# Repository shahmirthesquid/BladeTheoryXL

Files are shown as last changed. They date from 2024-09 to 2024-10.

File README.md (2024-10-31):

# BladeTheoryXL

Build log of my custom FPV drone built off an old Blade Theory XL
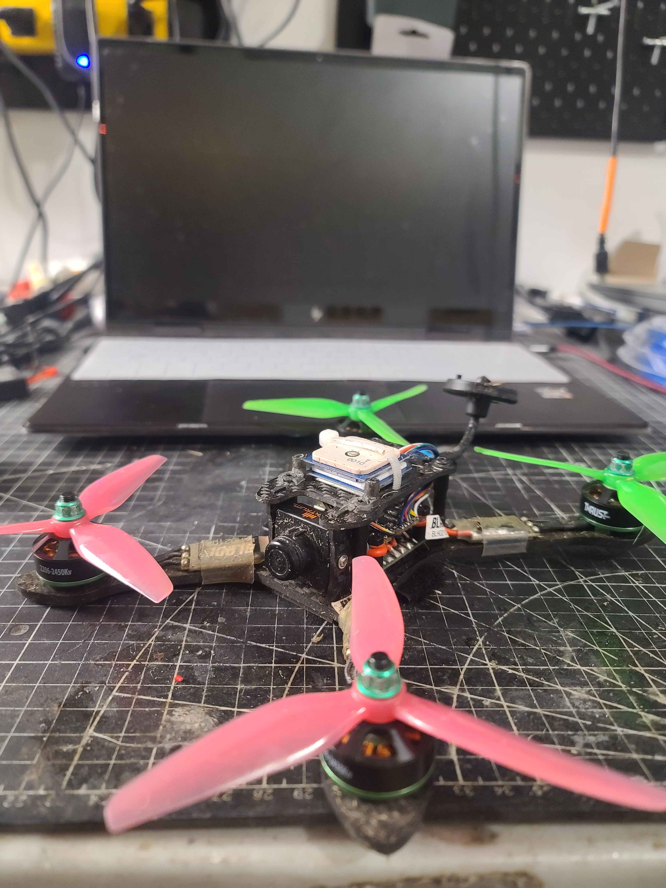
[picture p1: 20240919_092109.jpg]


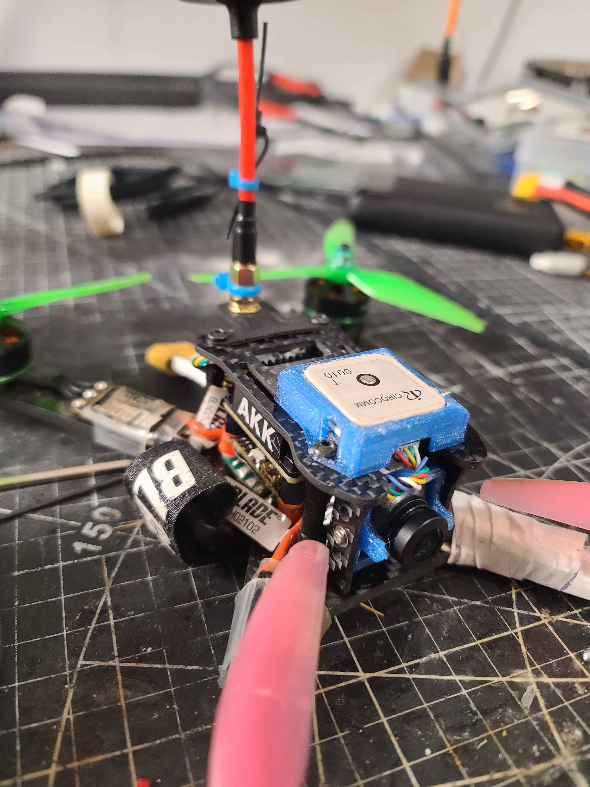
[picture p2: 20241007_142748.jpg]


https://www.bladehelis.com/product/theory-xl-5-fpv-bnf-basic/BLH02150.html

Archive of the above link can be found in this repo.

## Quick Overview

Frame: Blade Theory XL

Motors:Blade BLHA1023 Thrust Series 2206-2450Kv

ESC: 4 x Blade BLH02102 (FlyColor Fairy 30A)

Flight Controller: OMNIBUSF4SD w/ ICM42688P Gyro

VTX: AKK Ultra Long Range 3 Watt

Camera: Caddx Ratel 2

RX: SpeedyBee ELRS Nano

GPS: Beitan BN-880

Propellers: Ethix S3 Watermelon

Battery: 4S 1600mAh Lipo(10m Flight time) or 3S 4200mAh Molicel P42A pack (?m Flight time)

## Personal Tune and Config

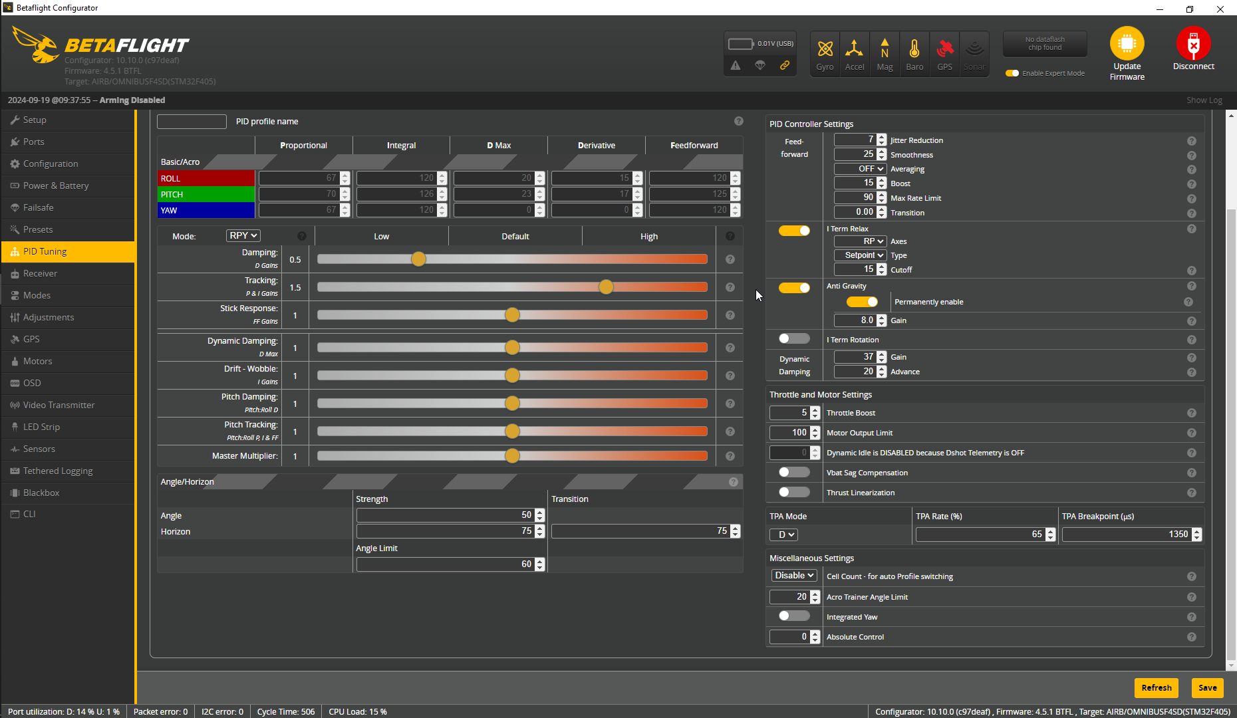
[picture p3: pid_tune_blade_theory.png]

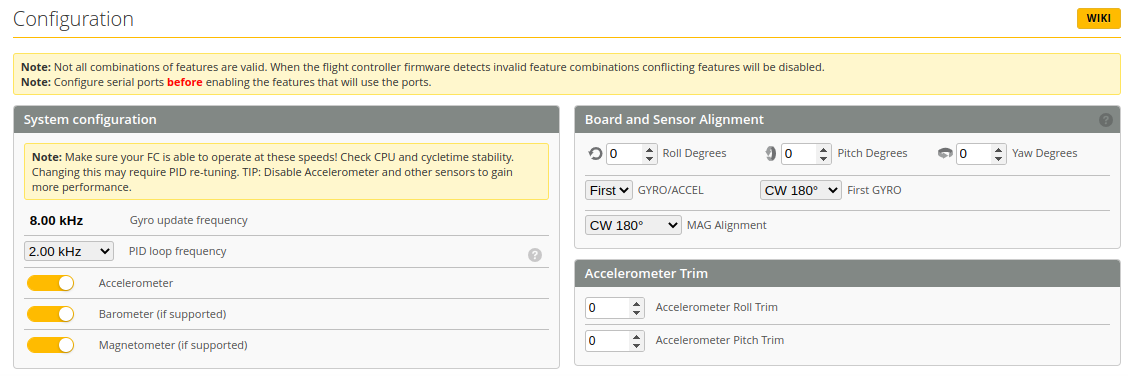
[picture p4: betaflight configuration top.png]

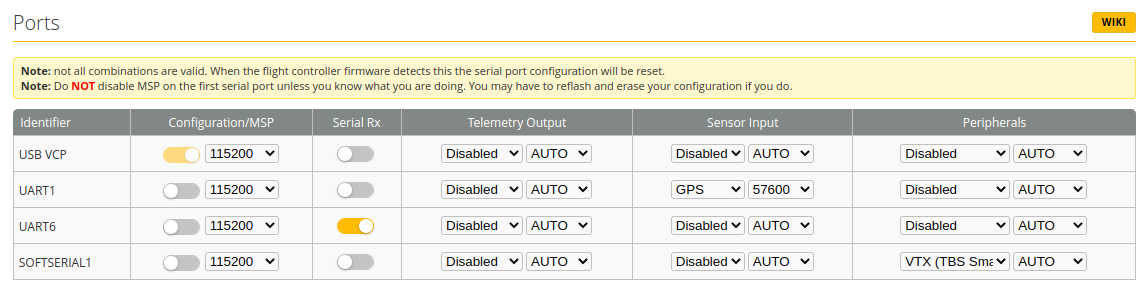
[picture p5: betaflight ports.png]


## Parts

### Frame
Stock 4mm carbon fiber Blade Theory XL frame.

### Flight Controller
Originally a Spektrum F3 controller but was replaced with F4V3S clone from aliexpress

https://www.aliexpress.com/item/1005005407722952.html



### Camera
Originally had a 700 TVL Spektrum camera. Wow this was such a bad camera. Terrible FOV and no OSD support.
Replacing with a CADDX Ratel 2. Currently waiting for it to arrive.

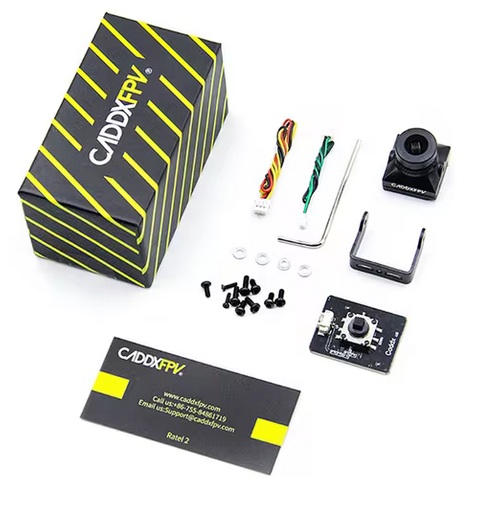
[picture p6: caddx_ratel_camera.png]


### Video Transmitter (VTX) 
Stock 200mw Spektrum VTX is actually quite nice. Range is very good for 200mw. Unfortunately you have to physically turn on the VTX button every flight. 

I am replacing this with AKK Long range 3W VTX. Currently waiting for it to arrive.

https://www.aliexpress.com/item/1005006955054449.html

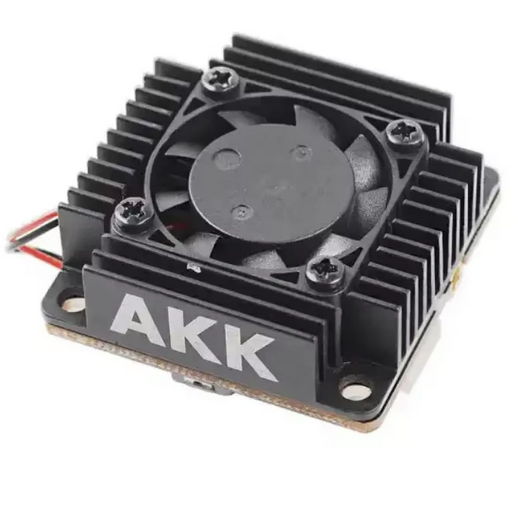
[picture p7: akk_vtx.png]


The AKK VTX seems really good. I put silicone conformal coating on it, and used SoftSerial to turn Motor5 pad into TX for the SmartAudio connection. I setup the VTX table, but had to manually set 5 bands in the table first. I then transferred the VTX switch settings from my Eachine Cvatar to be able to change VTX power using the 6 button switch at the top of my Jumper Tpro radio. 

Ultra Long Range VTX Table:
```
vtxtable channels 8
vtxtable band 1 BOSCAM_A A FACTORY 5865 5845 5825 5805 5785 5765 5745 5725
vtxtable band 2 BOSCAM_B B FACTORY 5733 5752 5771 5790 5809 5828 5847 5866
vtxtable band 3 BOSCAM_E E FACTORY 5705 5685 5665 0 5885 5905 0 0
vtxtable band 4 FATSHARK F FACTORY 5740 5760 5780 5800 5820 5840 5860 5880
vtxtable band 5 RACEBAND R FACTORY 5658 5695 5732 5769 5806 5843 5880 5917
vtxtable powerlevels 5
vtxtable powervalues 0 1 2 3 4
vtxtable powerlabels 250 500 1000 2000 3000
```

VTX Switch Based on Aux Channel 4:
```
vtx 0 3 0 0 1 1175 1375
vtx 1 3 0 0 2 1375 1525
vtx 2 3 0 0 3 1525 1650
vtx 3 3 0 0 5 1650 1850
```

This configuration changes VTX power based on the position of AUX channel 4. This skips the 2 watt setting on the VTX as I don't want to waste buttons to map out every power level. These buttons can then be reserved for future functionality.

### Reciever
Originally had a Spektrum SPM4649T / SH703X reciever that refused to go into bind mode.

Replaced with SpeedyBee ELRS Nano reciever from amazon

https://www.amazon.ca/dp/B0CTBWQ91P

### ESC
Stock power delivery board, and 30A BLHeli ESCS (BLH02102) running OneShot125 protocol.

ESCs are kinda bad, but after a custom tune they were alright. They didn't seem to have the precision of more modern ESCS using DSHOT protocol. 

I have the parts to replace these, but I'd like to ride these until they die so that I don't make ewaste.

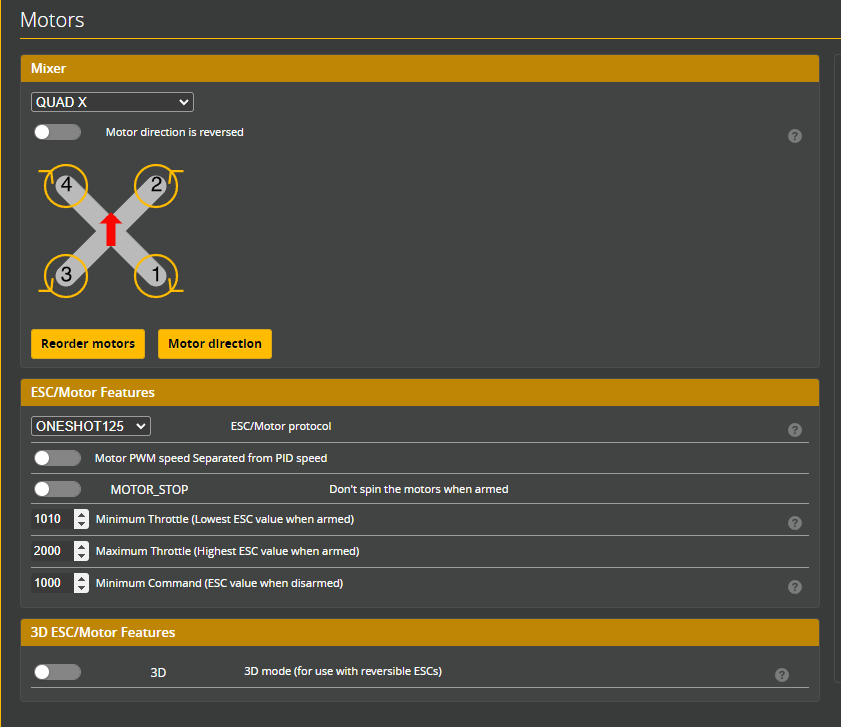
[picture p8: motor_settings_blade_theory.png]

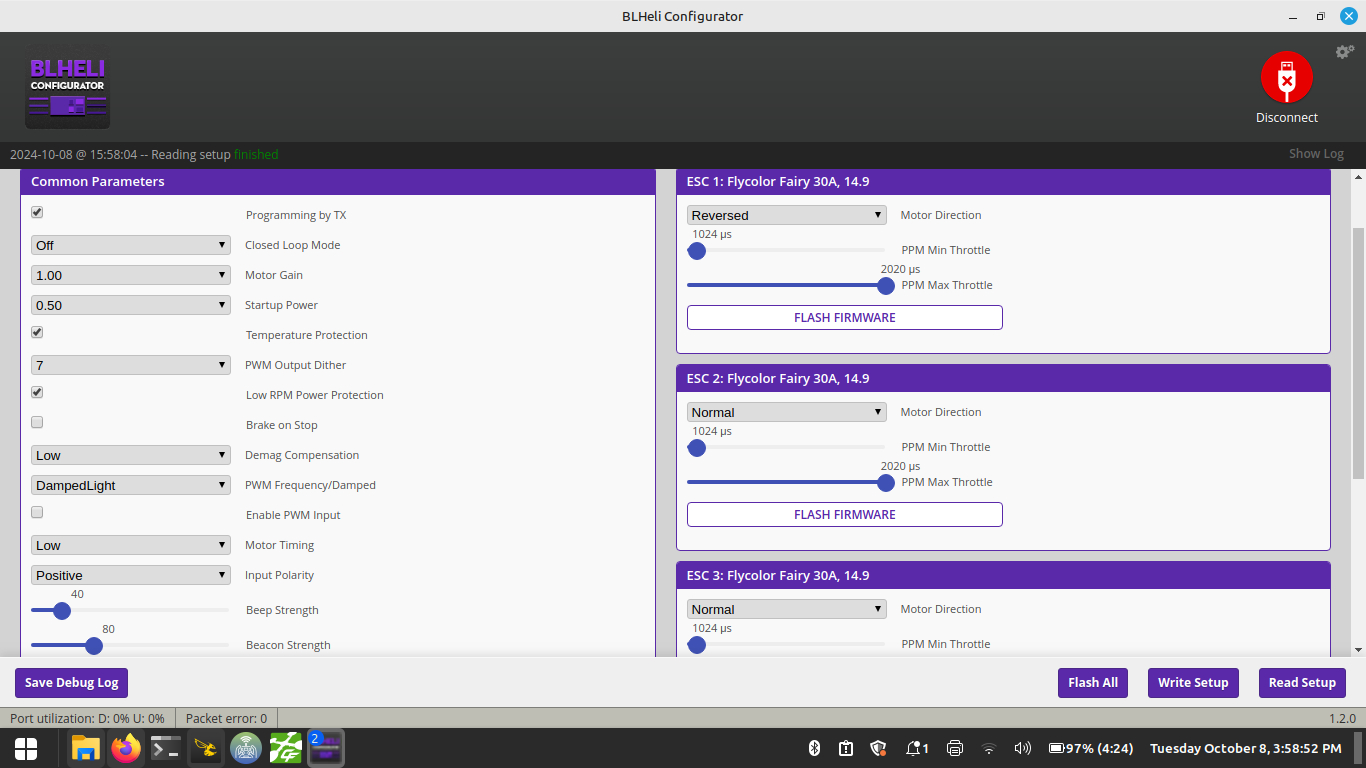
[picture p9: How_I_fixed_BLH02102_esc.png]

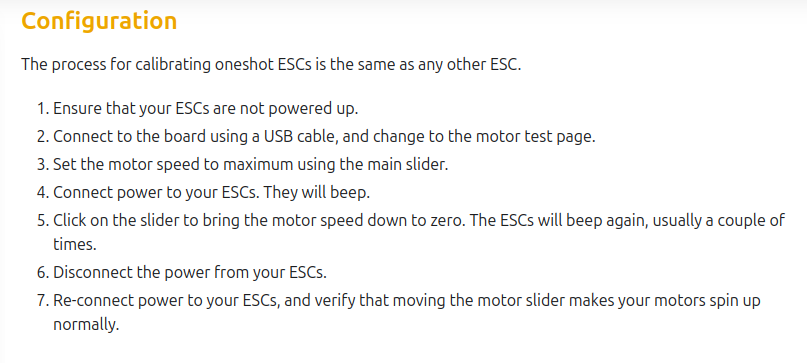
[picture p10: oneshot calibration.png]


### Motors
Stock 2206 size motors at 2450Kv

### GPS
Beitan BN-880 GPS unit for return to home failsafe functionality

Compass Setup:
```
resource SERIAL_TX 3 NONE
resource SERIAL_RX 3 NONE
resource I2C_SCL 2 B10
resource I2C_SDA 2 B11
set mag_bustype = I2C
set mag_i2c_device = 2
set mag_i2c_address = 0
set mag_spi_device = 0
set mag_hardware = AUTO
save
```

### VTX Mount 3D Print

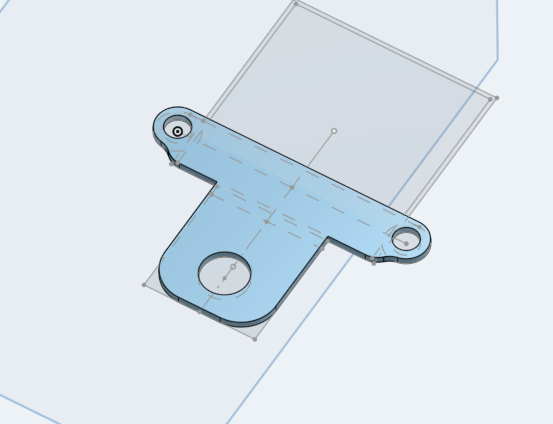
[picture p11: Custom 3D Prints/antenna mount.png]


https://www.thingiverse.com/thing:6790557

### GPS Mount 3D Print

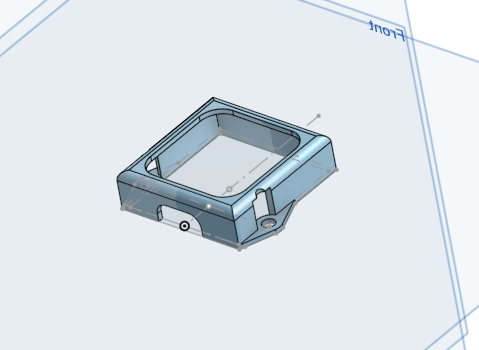
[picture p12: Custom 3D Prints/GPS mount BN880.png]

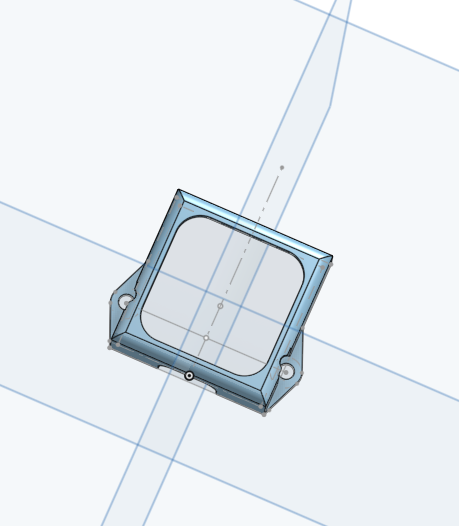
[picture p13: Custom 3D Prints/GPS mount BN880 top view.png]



https://www.thingiverse.com/thing:6790582

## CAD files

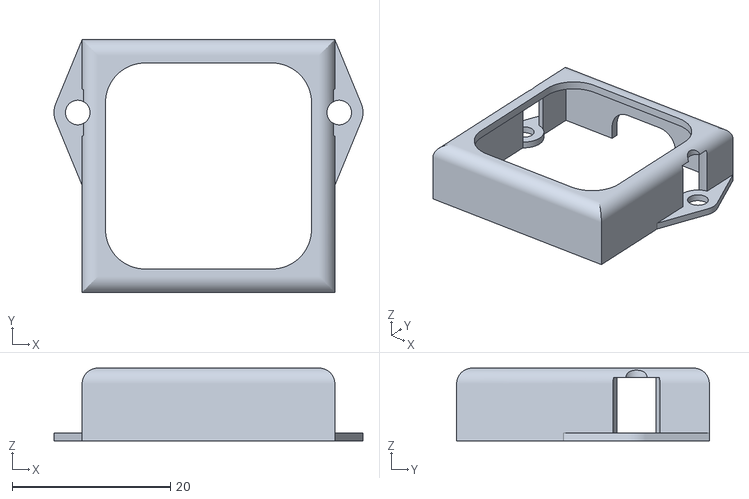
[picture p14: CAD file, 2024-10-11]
Custom 3D Prints/Blade Theory XL BN880 GPS mount By Shahmir Khan.stl
39.0 x 31.9 x 9.20

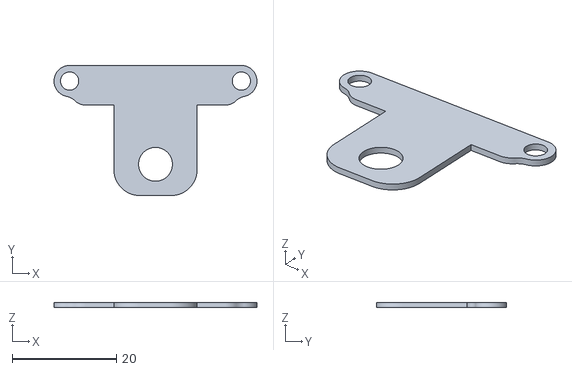
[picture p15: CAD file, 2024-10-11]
Custom 3D Prints/Blade Theory XL VTX Antenna Mount By Shahmir Khan.stl
39.0 x 25.0 x 1.00

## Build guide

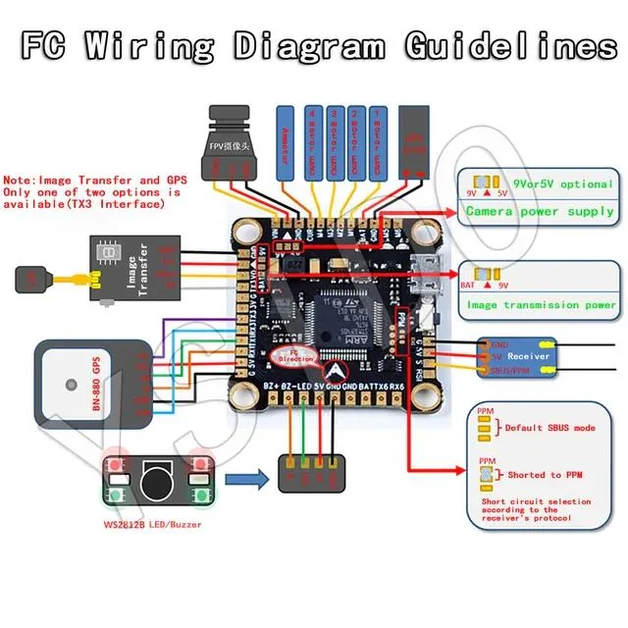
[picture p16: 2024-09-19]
f4v3s wiring diagram.webp

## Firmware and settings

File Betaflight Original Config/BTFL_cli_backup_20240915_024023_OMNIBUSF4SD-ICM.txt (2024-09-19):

# diff all defaults

# version
# Betaflight / STM32F405 (S405) 4.5.0 May 18 2024 / 14:33:50 () MSP API: 1.46

# start the command batch
batch start

# reset configuration to default settings
defaults nosave

board_name OMNIBUSF4SD-ICM
manufacturer_id AIRB
mcu_id 003800343333510632393735
signature 
#feature -SERVO_TILT
#feature -GPS
#feature -RANGEFINDER
#feature -TELEMETRY
#feature -LED_STRIP
#feature -DISPLAY
#feature -OSD
#feature -CHANNEL_FORWARDING
#feature -TRANSPONDER

# feature
feature SERVO_TILT
feature GPS
feature RANGEFINDER
feature TELEMETRY
feature LED_STRIP
feature DISPLAY
feature OSD
feature CHANNEL_FORWARDING
feature TRANSPONDER

# serial
#serial 0 0 115200 57600 0 115200
serial 0 2 115200 57600 0 115200

# aux
#aux 0 0 0 900 900 0 0
aux 0 0 0 1675 2100 0 0
#aux 1 0 0 900 900 0 0
aux 1 1 1 900 1700 0 0
#aux 2 0 0 900 900 0 0
aux 2 2 1 1700 2100 0 0
#aux 3 0 0 900 900 0 0
aux 3 19 2 1700 2100 0 0

# master
#set gyro_lpf1_static_hz = 250
set gyro_lpf1_static_hz = 300
#set gyro_lpf2_static_hz = 500
set gyro_lpf2_static_hz = 600
#set dyn_notch_min_hz = 100
set dyn_notch_min_hz = 125
#set dyn_notch_max_hz = 600
set dyn_notch_max_hz = 650
#set gyro_lpf1_dyn_min_hz = 250
set gyro_lpf1_dyn_min_hz = 300
#set gyro_lpf1_dyn_max_hz = 500
set gyro_lpf1_dyn_max_hz = 600
#set acc_calibration = 0,0,0,0
set acc_calibration = 12,-29,40,1
#set mag_i2c_device = 2
set mag_i2c_device = 1
#set min_check = 1050
set min_check = 1000
#set min_throttle = 1070
set min_throttle = 1000
#set motor_pwm_protocol = DSHOT600
set motor_pwm_protocol = ONESHOT125
#set pid_process_denom = 1
set pid_process_denom = 4
#set simplified_gyro_filter_multiplier = 100
set simplified_gyro_filter_multiplier = 120
#set osd_flymode_pos = 341
set osd_flymode_pos = 2137
#set osd_gps_sats_pos = 341
set osd_gps_sats_pos = 2117
#set osd_altitude_pos = 341
set osd_altitude_pos = 2149
#set osd_avg_cell_voltage_pos = 341
set osd_avg_cell_voltage_pos = 2565

profile 0

# profile 0
#set dterm_lpf1_dyn_min_hz = 75
set dterm_lpf1_dyn_min_hz = 90
#set dterm_lpf1_dyn_max_hz = 150
set dterm_lpf1_dyn_max_hz = 180
#set dterm_lpf1_static_hz = 75
set dterm_lpf1_static_hz = 90
#set dterm_lpf2_static_hz = 150
set dterm_lpf2_static_hz = 180
#set pidsum_limit = 500
set pidsum_limit = 1000
#set pidsum_limit_yaw = 400
set pidsum_limit_yaw = 1000
#set yaw_lowpass_hz = 100
set yaw_lowpass_hz = 0
#set p_pitch = 47
set p_pitch = 51
#set i_pitch = 84
set i_pitch = 92
#set d_pitch = 46
set d_pitch = 34
#set f_pitch = 125
set f_pitch = 162
#set p_roll = 45
set p_roll = 49
#set i_roll = 80
set i_roll = 88
#set d_roll = 40
set d_roll = 30
#set f_roll = 120
set f_roll = 156
#set p_yaw = 45
set p_yaw = 49
#set i_yaw = 80
set i_yaw = 88
#set f_yaw = 120
set f_yaw = 156
#set simplified_pi_gain = 100
set simplified_pi_gain = 110
#set simplified_dmax_gain = 100
set simplified_dmax_gain = 0
#set simplified_feedforward_gain = 100
set simplified_feedforward_gain = 130
#set simplified_dterm_filter_multiplier = 100
set simplified_dterm_filter_multiplier = 120
#set ez_landing_limit = 15
set ez_landing_limit = 5

profile 1

profile 2

profile 3

# restore original profile selection
profile 0

rateprofile 0

rateprofile 1

rateprofile 2

rateprofile 3

# restore original rateprofile selection
rateprofile 0

# save configuration
save

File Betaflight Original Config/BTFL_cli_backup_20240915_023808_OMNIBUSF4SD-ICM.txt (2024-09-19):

defaults nosave


# version
# Betaflight / STM32F405 (S405) 4.5.0 May 18 2024 / 14:33:50 () MSP API: 1.46

# start the command batch
batch start

# reset configuration to default settings
defaults nosave

board_name OMNIBUSF4SD-ICM
manufacturer_id AIRB
mcu_id 003800343333510632393735
signature 

# feature
feature SERVO_TILT
feature GPS
feature RANGEFINDER
feature TELEMETRY
feature LED_STRIP
feature DISPLAY
feature OSD
feature CHANNEL_FORWARDING
feature TRANSPONDER

# serial
serial 0 2 115200 57600 0 115200

# aux
aux 0 0 0 1675 2100 0 0
aux 1 1 1 900 1700 0 0
aux 2 2 1 1700 2100 0 0
aux 3 19 2 1700 2100 0 0

# master
set gyro_lpf1_static_hz = 300
set gyro_lpf2_static_hz = 600
set dyn_notch_min_hz = 125
set dyn_notch_max_hz = 650
set gyro_lpf1_dyn_min_hz = 300
set gyro_lpf1_dyn_max_hz = 600
set acc_calibration = 12,-29,40,1
set mag_i2c_device = 1
set min_check = 1000
set min_throttle = 1000
set motor_pwm_protocol = ONESHOT125
set pid_process_denom = 4
set simplified_gyro_filter_multiplier = 120
set osd_flymode_pos = 2137
set osd_gps_sats_pos = 2117
set osd_altitude_pos = 2149
set osd_avg_cell_voltage_pos = 2565

profile 0

# profile 0
set dterm_lpf1_dyn_min_hz = 90
set dterm_lpf1_dyn_max_hz = 180
set dterm_lpf1_static_hz = 90
set dterm_lpf2_static_hz = 180
set pidsum_limit = 1000
set pidsum_limit_yaw = 1000
set yaw_lowpass_hz = 0
set p_pitch = 51
set i_pitch = 92
set d_pitch = 34
set f_pitch = 162
set p_roll = 49
set i_roll = 88
set d_roll = 30
set f_roll = 156
set p_yaw = 49
set i_yaw = 88
set f_yaw = 156
set simplified_pi_gain = 110
set simplified_dmax_gain = 0
set simplified_feedforward_gain = 130
set simplified_dterm_filter_multiplier = 120
set ez_landing_limit = 5

profile 1

profile 2

profile 3

# restore original profile selection
profile 0

rateprofile 0

rateprofile 1

rateprofile 2

rateprofile 3

# restore original rateprofile selection
rateprofile 0

# save configuration

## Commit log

2024-09-19 Added pics
    Added main pic and wiring diagram
2024-09-19 Added Backups
    [BTFL_cli_backup_20240915_023808_OMNIBUSF4SD-ICM.txt, BTFL_cli_backup_20240915_024023_OMNIBUSF4SD-ICM.txt]
2024-10-11 Add 3D prints
    [Blade Theory XL BN880 GPS mount By Shahmir Khan.stl, Blade Theory XL VTX Antenna Mount By Shahmir Khan.stl]
